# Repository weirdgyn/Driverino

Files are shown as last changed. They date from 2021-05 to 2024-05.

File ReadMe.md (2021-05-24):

# Driverino 

### (italian noun) /ˈdraɪvərnəʊ/ : *little driver*

Driverino is a pretty simple, low power, driver for [BLDC](https://en.wikipedia.org/wiki/Brushless_DC_electric_motor) sensored motors.
The project target was to create a very small unit capable of driving a motor rated about 50-100W.
The board is fitted with ATmega32U4 micro the same of Arduino Micro Pro commercial boards, once the correct bootloader has been burned-in the board should act as an Arduino board (at least for programming/debugging task) and also spin a motor.
The project includes:
 1. Fully designed 2 layers PCB board (KiCAD);
 2. Driverino firmware sources;
 3. MCT8316Z library sources.

Driverino's firmware allow users to drive BLDC motors using a standard [RS232](https://en.wikipedia.org/wiki/RS-232) interface trough simple interactive commands.
The firmware allows also:
* closed loop speed control (implementing a [PID](https://en.wikipedia.org/wiki/PID_controller) loop);
* motor/driver status monitoring;
* R/C ESC emulation.

The library allows Arduino users to interact with BLDC motors without knowledge of MCT8316Z chip and [SPI](https://en.wikipedia.org/wiki/Serial_Peripheral_Interface) protocol.

## Driverino features

* ATmega32U4 microcontroller;
* Micro [USB](https://en.wikipedia.org/wiki/USB) interface;
* MCT8316Z motor driver;
* 41x26mm (size);
* RS232 interface;
* Standard R/C input compatibile.

The board can drive up to 24V-36V 8A rated sensored BLDC motors and provide 5V power supply (200mA max) mimicking R/C ESC BEC feature.
Driverino supports a variety of different types of [Hall](https://en.wikipedia.org/wiki/Hall_effect_sensor)'s sensors (analog single ended, analog differtial, digital) and also different sensors supply rates (3.3V and 5V). To correctly fit for a specific sensor kind some soldering may be required: by default the board project is fitted for digital 5V sensors.

## Firmware

TBD

## Library

TBD

# TODO:

- [ ] Add features:
   - [ ] vm measurement;
   - [ ] current measurement (via INA250).
- [ ] Optimize PCB layout.
- [ ] Write Library.
- [ ] Write Firmware.
- [ ] Submit to Kitspace
- [ ] Submit to Made-With-KiCAD

# Links

* [Atmel/Microchip ATMega32U4](https://www.microchip.com/wwwproducts/en/ATmega32U4)
* [TI MCT8316Z](https://www.ti.com/product/MCT8316Z?keyMatch=MCT8316Z&tisearch=search-everything)
* [Arduino](https://www.arduino.cc/)
* [KiCAD](https://www.kicad.org/)

#

Live long and prosper!

That's all folks.

By[t]e{s} Weirdgyn

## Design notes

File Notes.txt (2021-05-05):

C15 10uF 50V X7R (1206) -> 35V X5R (0805)

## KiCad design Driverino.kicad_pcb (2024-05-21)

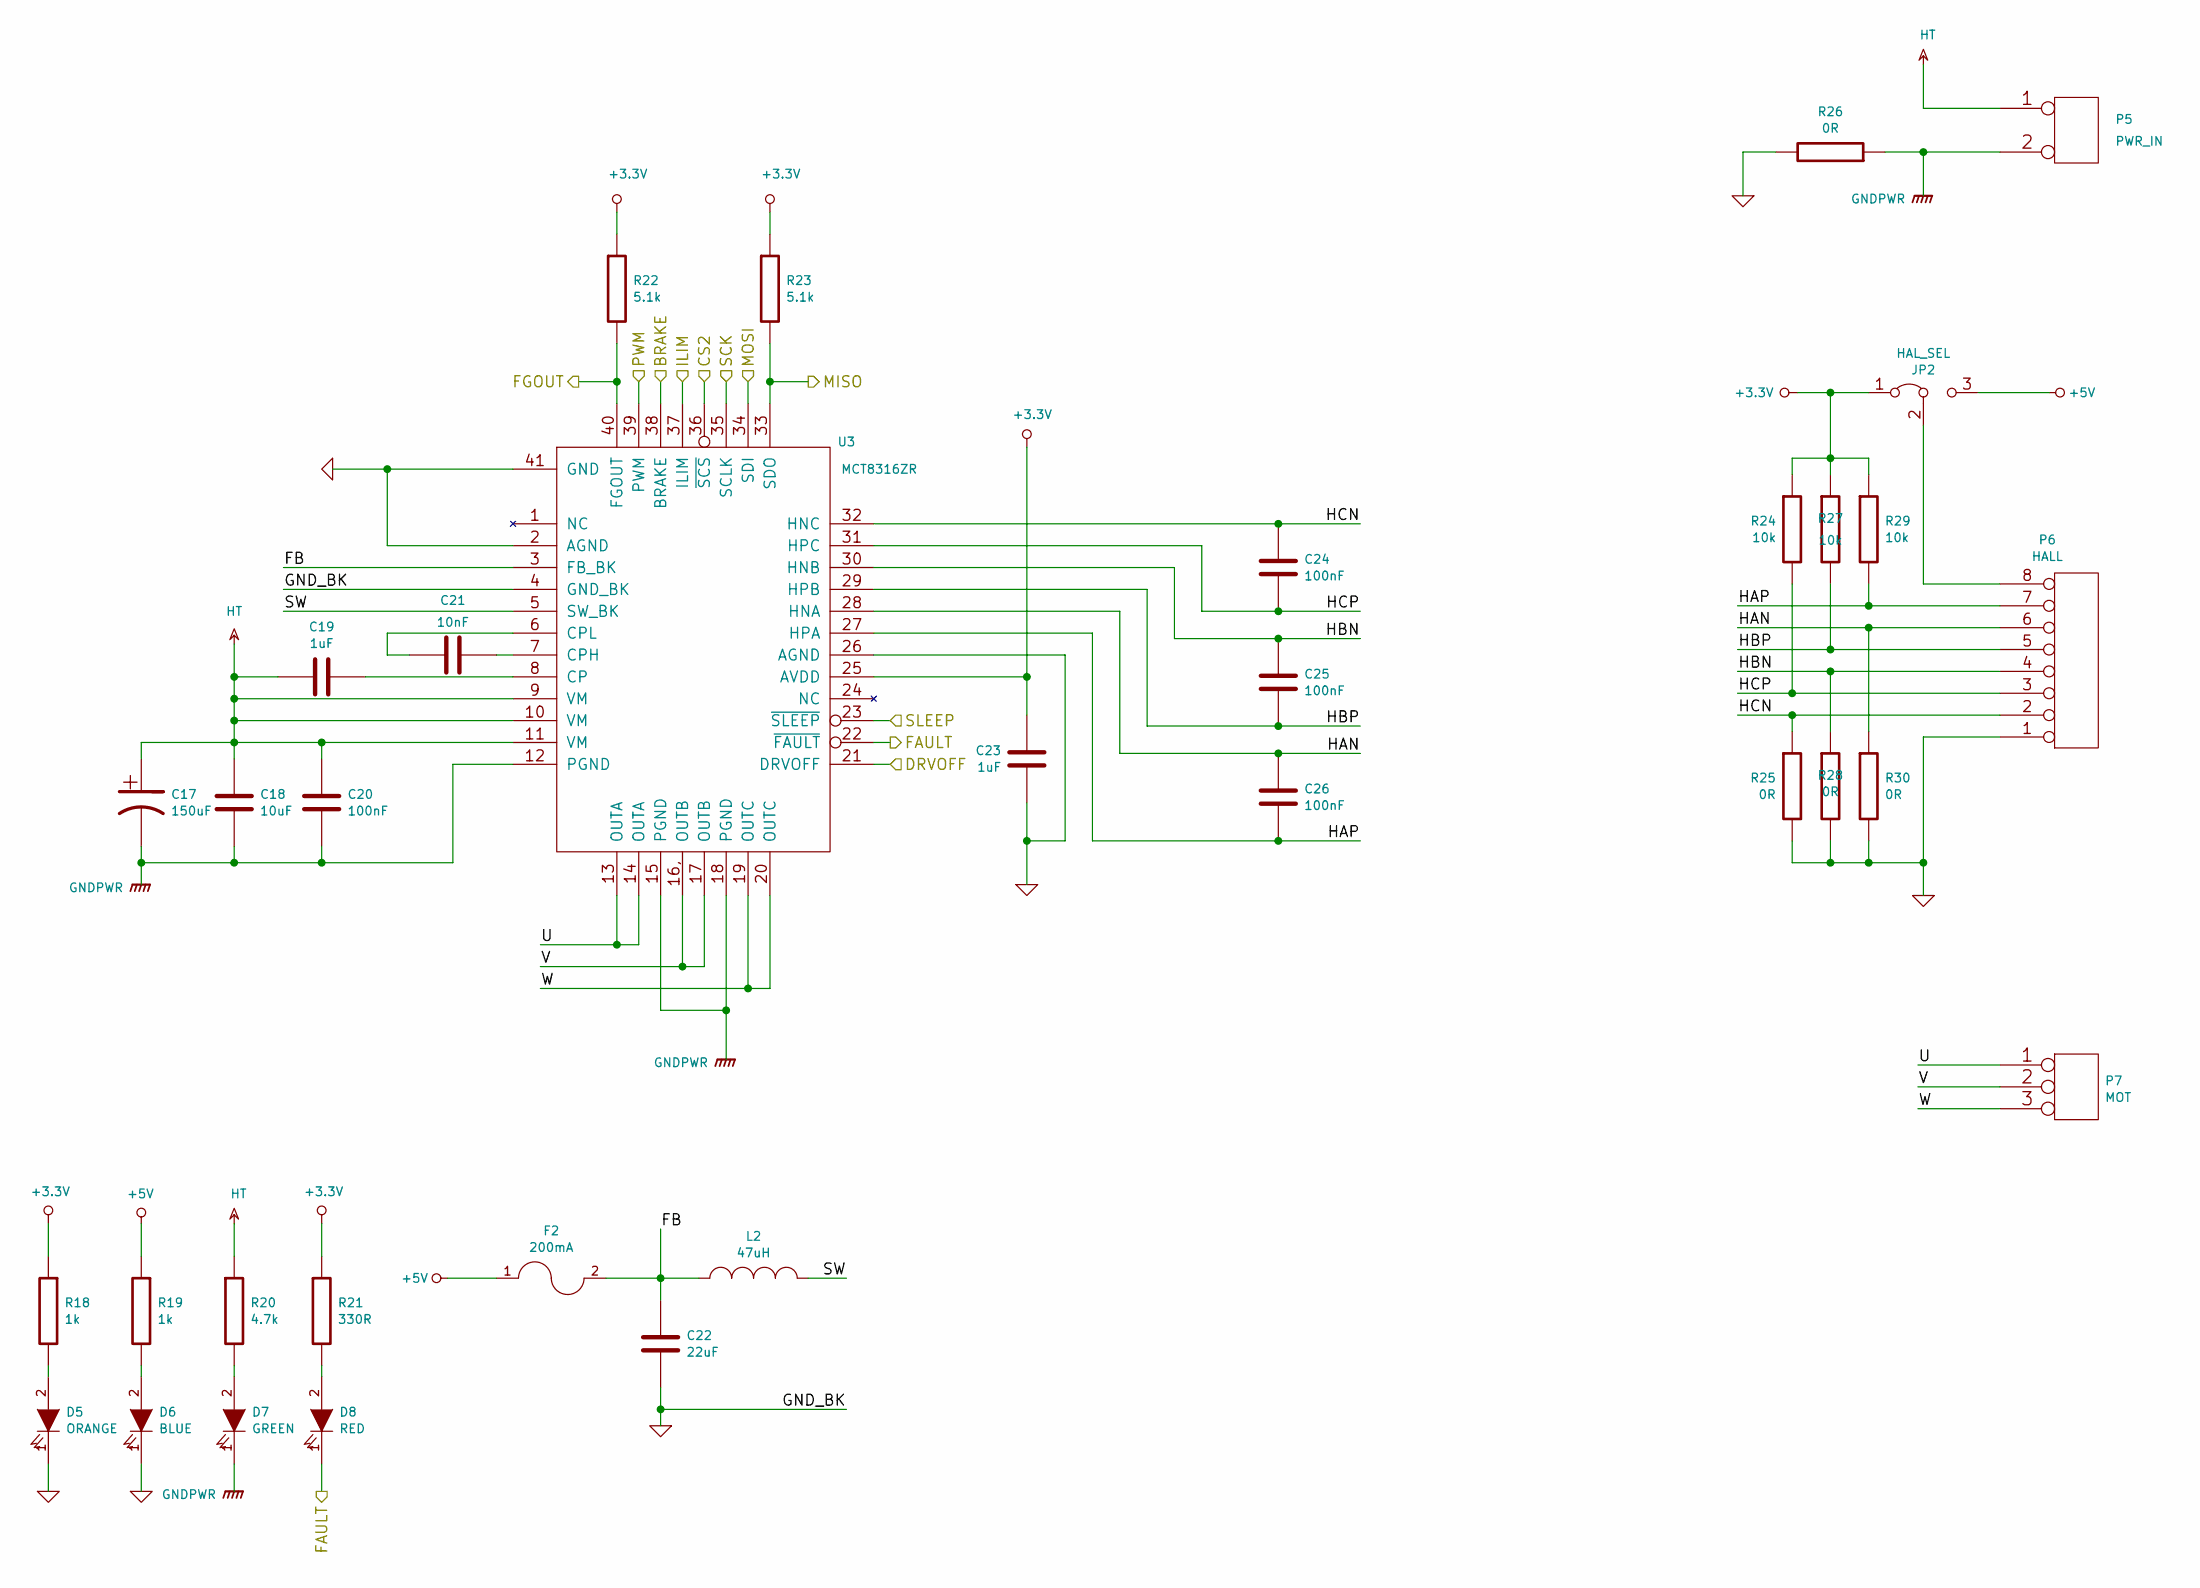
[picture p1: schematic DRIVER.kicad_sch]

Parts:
C17: 150uF; CP_Elec_6.3x7.7
C18: 10uF; C_1206_3216Metric
C19, C23: 1uF; C_0603_1608Metric
C20, C24, C25, C26: 100nF; C_0402_1005Metric
C21: 10nF; C_0402_1005Metric
C22: 22uF; C_1206_3216Metric
D5: ORANGE; LED_0603_1608Metric
D6: BLUE; LED_0603_1608Metric
D7: GREEN; LED_0603_1608Metric
D8: RED; LED_0603_1608Metric
F2: 200mA; Fuse_0402_1005Metric
JP2: HAL_SEL; PinHeader_1x03_P1.27mm_Vertical
L2: 47uH; L_1210_3225Metric
P5: PWR_IN; 39773-0002
P6: HALL; Molex_PicoBlade_53047-0810_1x08_P1.25mm_Vertical
P7: MOT; 39773-0003
R18, R19: 1k; R_0402_1005Metric
R20: 4.7k; R_0402_1005Metric
R21: 330R; R_0402_1005Metric
R22, R23: 5.1k; R_0402_1005Metric
R24, R27, R29: 10k; R_0402_1005Metric
R25, R26, R28, R30: 0R; R_0402_1005Metric
U3: MCT8316ZR; QFN-40_EP_5x7_Pitch0.5mm

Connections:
+3.3V: C23.2, JP2.1 (A), R18.1, R21.1, R22.1, R23.1, R24.1, R27.1, R29.1, U3.25 (AVDD)
+5V: F2.1, JP2.3 (B), R19.1; also elsewhere on the board
/ARDUINO-MICRO/BRAKE: U3.38 (BRAKE); also elsewhere on the board
/ARDUINO-MICRO/CS2: U3.36 (~SCS); also elsewhere on the board
/ARDUINO-MICRO/DRVOFF: U3.21 (DRVOFF); also elsewhere on the board
/ARDUINO-MICRO/FAULT: D8.1 (K), U3.22 (~FAULT); also elsewhere on the board
/ARDUINO-MICRO/FGOUT: R22.2, U3.40 (FGOUT); also elsewhere on the board
/ARDUINO-MICRO/ILIM: U3.37 (ILIM); also elsewhere on the board
/ARDUINO-MICRO/MISO: R23.2, U3.33 (SDO); also elsewhere on the board
/ARDUINO-MICRO/MOSI: U3.34 (SDI); also elsewhere on the board
/ARDUINO-MICRO/PWM: U3.39 (PWM); also elsewhere on the board
/ARDUINO-MICRO/SCK: U3.35 (SCLK); also elsewhere on the board
/DRIVER/FB: C22.2, F2.2, L2.2, U3.3 (FB_BK)
/DRIVER/HAN: C26.2, P6.6, R30.1, U3.28 (HNA)
/DRIVER/HAP: C26.1, P6.7, R29.2, U3.27 (HPA)
/DRIVER/HBN: C25.2, P6.4, R28.1, U3.30 (HNB)
/DRIVER/HBP: C25.1, P6.5, R27.2, U3.29 (HPB)
/DRIVER/HCN: C24.2, P6.2, R25.1, U3.32 (HNC)
/DRIVER/HCP: C24.1, P6.3, R24.2, U3.31 (HPC)
/DRIVER/SLEEP: U3.23 (~SLEEP)
/DRIVER/SW: L2.1, U3.5 (SW_BK)
/DRIVER/U: P7.1, U3.13 (OUTA), U3.14 (OUTA)
/DRIVER/V: P7.2 (PM), U3.16, U3.16, (OUTB), U3.17 (OUTB)
/DRIVER/W: P7.3, U3.19 (OUTC), U3.20 (OUTC)
GND: C22.1, C23.1, D5.1 (K), D6.1 (K), P6.1, R25.2, R26.2, R28.2, R30.2, U3.2 (AGND), U3.4 (GND_BK), U3.26 (AGND), U3.41 (GND); also elsewhere on the board
GNDPWR: C17.2, C18.2, C20.2, D7.1 (K), P5.2 (PM), R26.1, U3.12 (PGND), U3.15 (PGND), U3.18 (PGND)
HT: C17.1, C18.1, C19.2, C20.1, P5.1, R20.1, U3.9 (VM), U3.10 (VM), U3.11 (VM)
unnamed: C19.1, U3.8 (CP)
unnamed: C21.1, U3.7 (CPH)
unnamed: C21.2, U3.6 (CPL)
unnamed: D5.2 (A), R18.2
unnamed: D6.2 (A), R19.2
unnamed: D7.2 (A), R20.2
unnamed: D8.2 (A), R21.2
unnamed: JP2.2 (C), P6.8

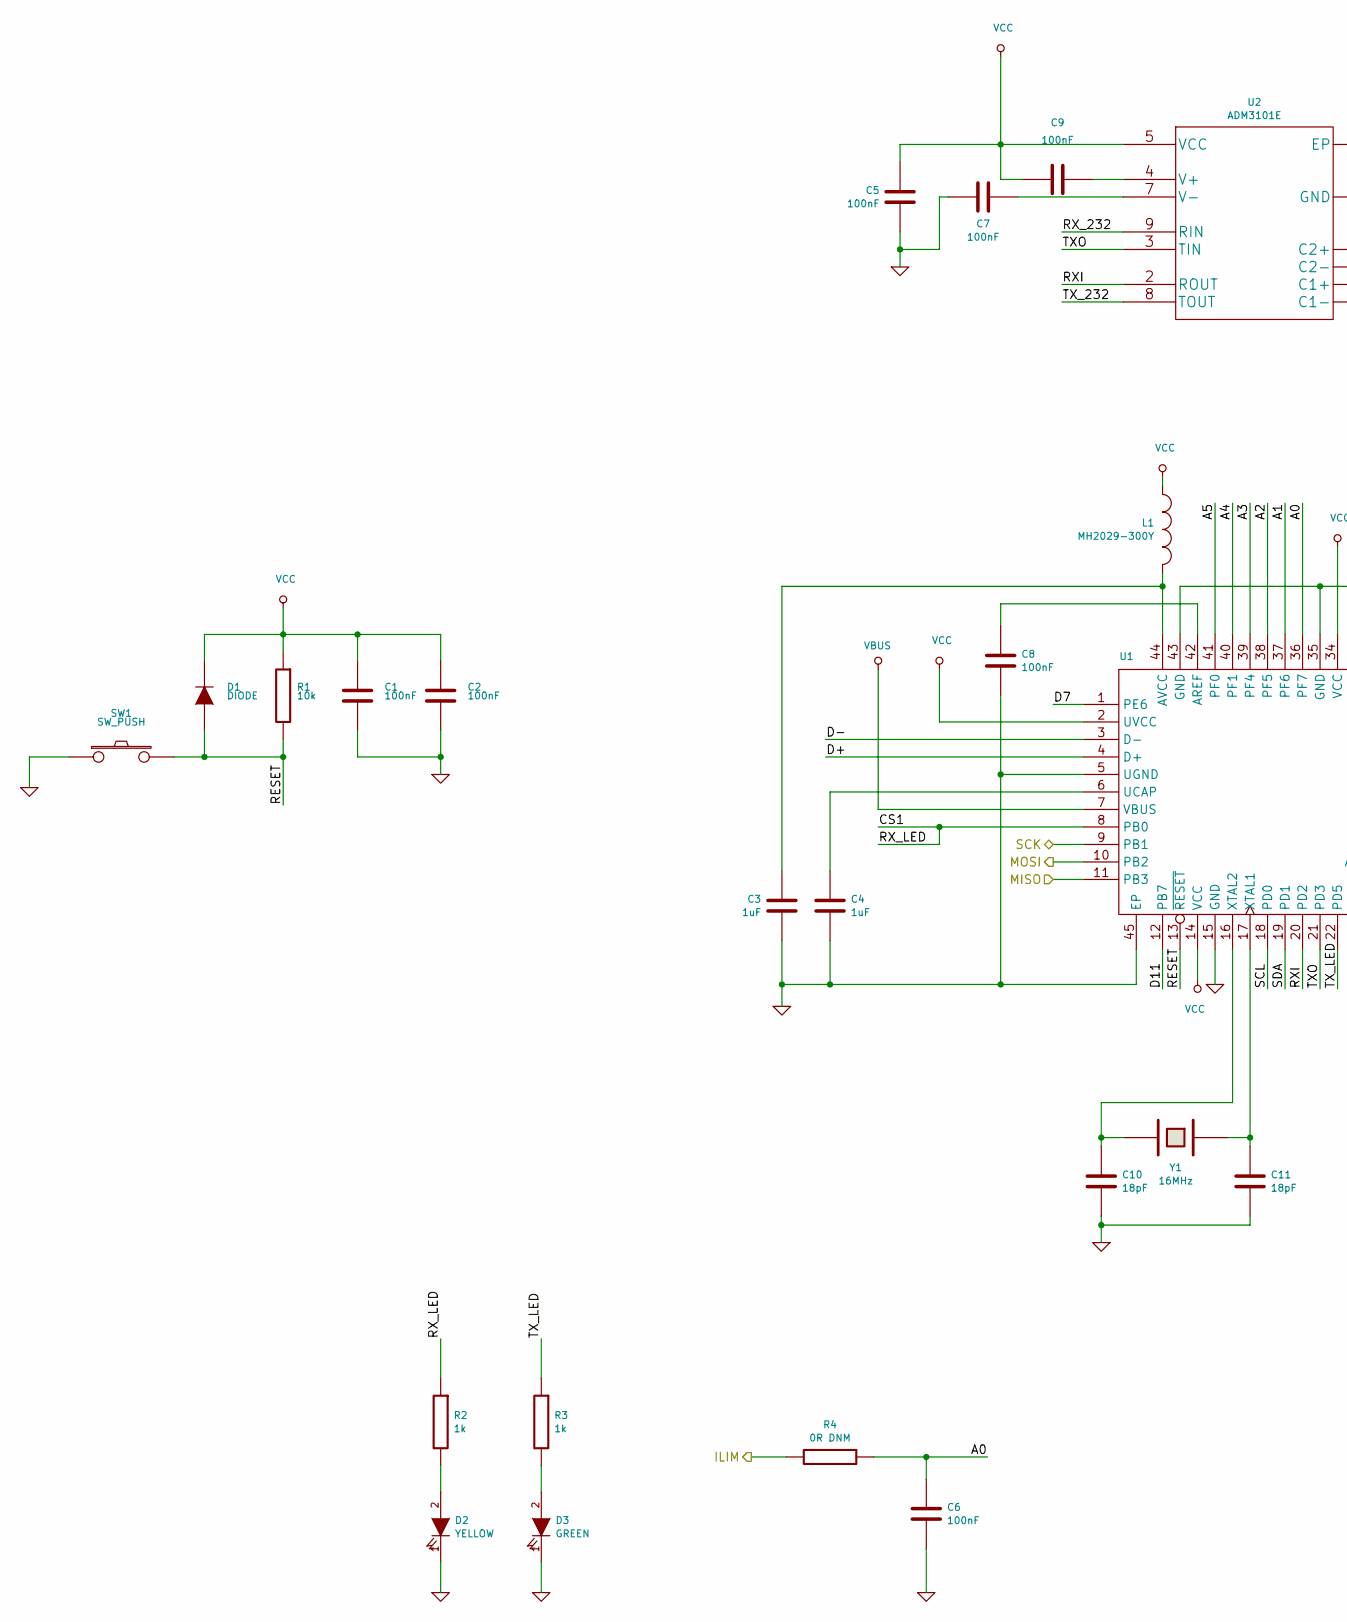
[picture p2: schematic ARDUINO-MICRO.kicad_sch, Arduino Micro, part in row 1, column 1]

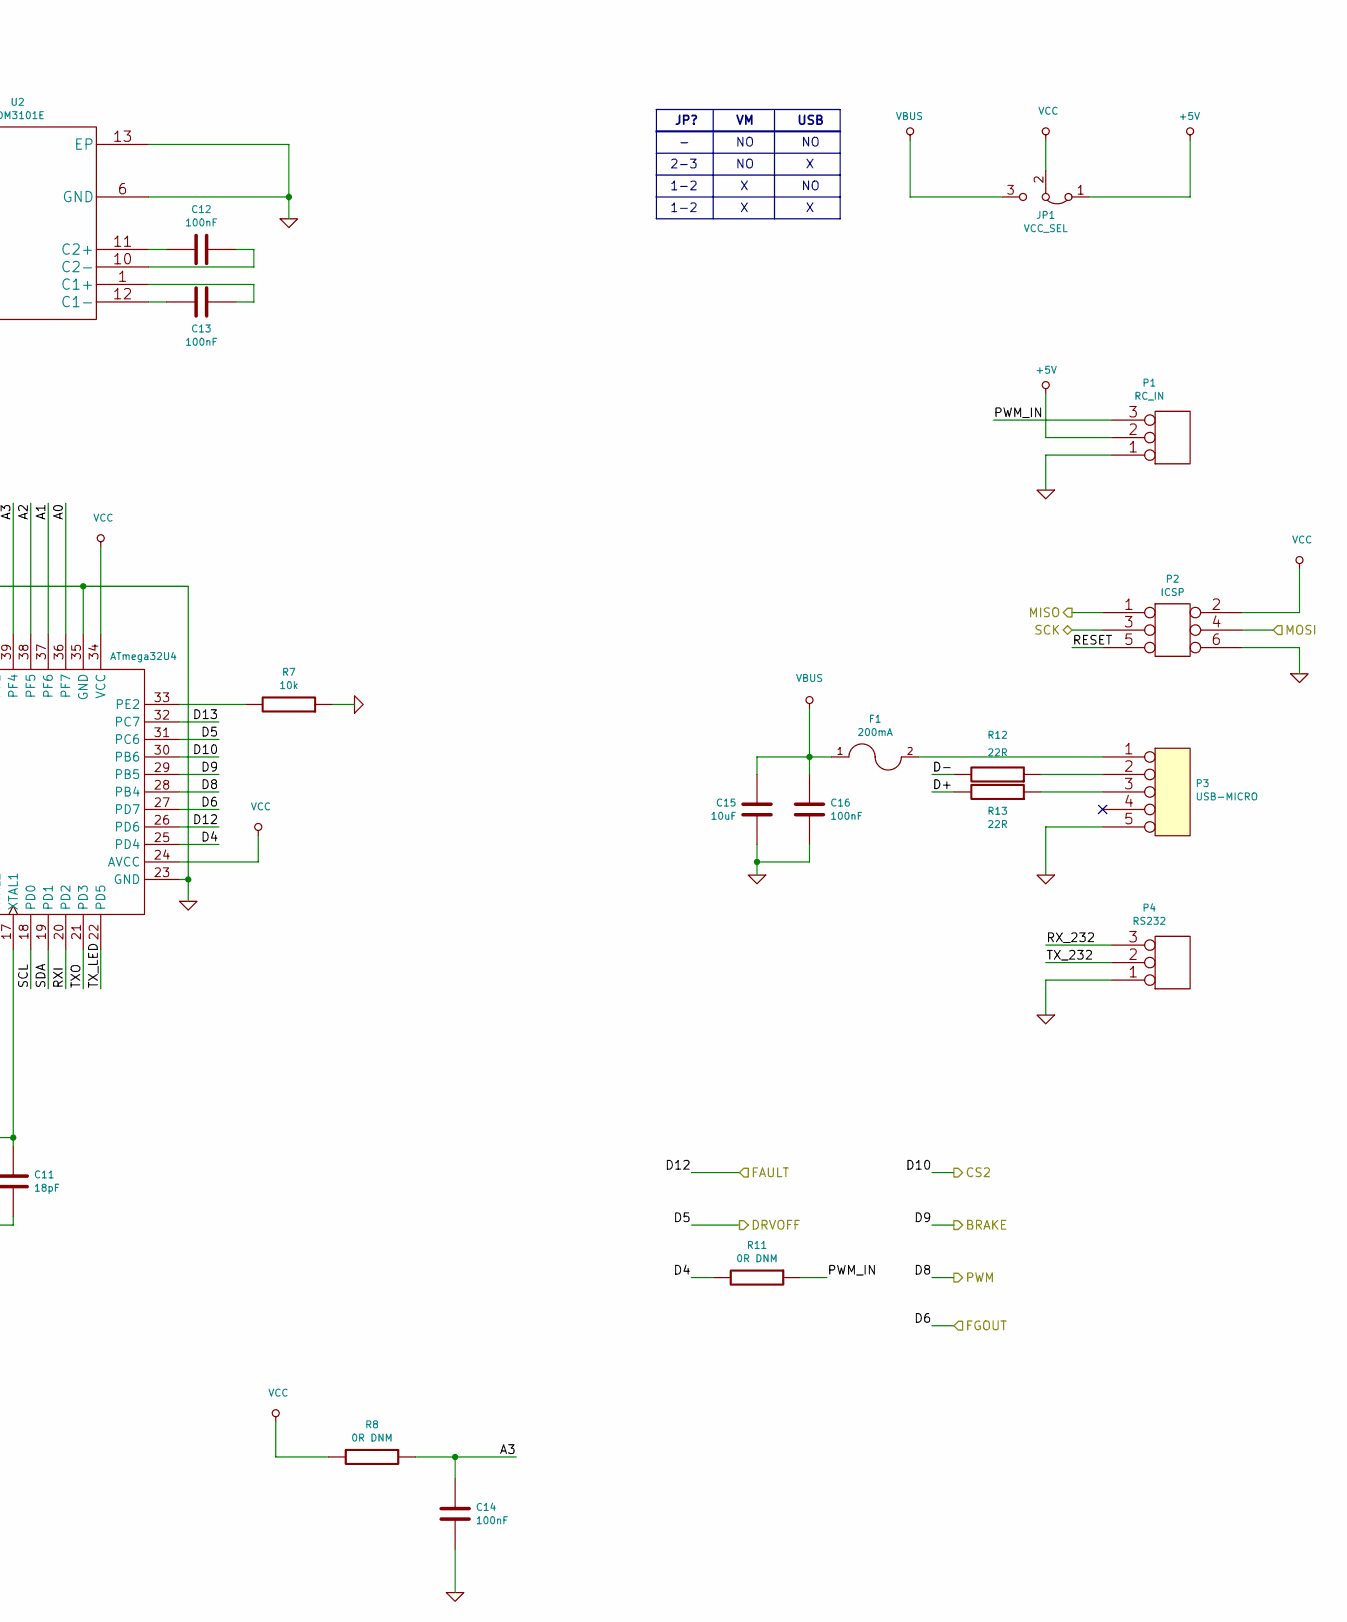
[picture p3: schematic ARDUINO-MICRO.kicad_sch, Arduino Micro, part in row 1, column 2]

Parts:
C1, C2, C5, C6, C7, C8, C9, C12, C13, C14, C16: 100nF; C_0402_1005Metric
C3, C4: 1uF; C_0603_1608Metric
C10, C11: 18pF; C_0402_1005Metric
C15: 10uF; C_1206_3216Metric
D1: DIODE; D_0402_1005Metric
D2: YELLOW; LED_0603_1608Metric
D3: GREEN; LED_0603_1608Metric
F1: 200mA; Fuse_0402_1005Metric
JP1: VCC_SEL; PinHeader_1x03_P1.27mm_Vertical
L1: MH2029-300Y; R_0805_2012Metric
P1: RC_IN; PinHeader_1x03_P2.54mm_Horizontal
P2: ICSP; PinHeader_2x03_P2.54mm_Vertical
P3: USB-MICRO; USB_Micro-B_Amphenol_10103594-0001LF_Horizontal
P4: RS232; Molex_PicoBlade_53047-0310_1x03_P1.25mm_Vertical
R1, R7: 10k; R_0402_1005Metric
R2, R3: 1k; R_0402_1005Metric
R4, R8, R11: 0R DNM; R_0402_1005Metric
R12, R13: 22R; R_0402_1005Metric
SW1: SW_PUSH; SW_SPST_B3U-1000P
U1: ATmega32U4; QFN-44-1EP_7x7mm_P0.5mm_EP5.2x5.2mm
U2: ADM3101E; CP-12-4
Y1: 16MHz; Crystal_SMD_2016-4Pin_2.0x1.6mm

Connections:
+5V: JP1.1 (A), P1.2 (PM); also elsewhere on the board
/ARDUINO-MICRO/A0: C6.2, R4.1, U1.36 (PF7)
/ARDUINO-MICRO/A1: U1.37 (PF6)
/ARDUINO-MICRO/A2: U1.38 (PF5)
/ARDUINO-MICRO/A3: C14.2, R8.1, U1.39 (PF4)
/ARDUINO-MICRO/A4: U1.40 (PF1)
/ARDUINO-MICRO/A5: U1.41 (PF0)
/ARDUINO-MICRO/BRAKE: U1.29 (PB5); also elsewhere on the board
/ARDUINO-MICRO/CS1: R2.1, U1.8 (PB0)
/ARDUINO-MICRO/CS2: U1.30 (PB6); also elsewhere on the board
/ARDUINO-MICRO/D4: R11.2, U1.25 (PD4)
/ARDUINO-MICRO/D7: U1.1 (PE6)
/ARDUINO-MICRO/D11: U1.12 (PB7)
/ARDUINO-MICRO/D13: U1.32 (PC7)
/ARDUINO-MICRO/D+: R13.2, U1.4 (D+)
/ARDUINO-MICRO/D-: R12.2, U1.3 (D-)
/ARDUINO-MICRO/DRVOFF: U1.31 (PC6); also elsewhere on the board
/ARDUINO-MICRO/FAULT: U1.26 (PD6); also elsewhere on the board
/ARDUINO-MICRO/FGOUT: U1.27 (PD7); also elsewhere on the board
/ARDUINO-MICRO/ILIM: R4.2; also elsewhere on the board
/ARDUINO-MICRO/MISO: P2.1, U1.11 (PB3); also elsewhere on the board
/ARDUINO-MICRO/MOSI: P2.4, U1.10 (PB2); also elsewhere on the board
/ARDUINO-MICRO/PWM: U1.28 (PB4); also elsewhere on the board
/ARDUINO-MICRO/PWM_IN: P1.3, R11.1
/ARDUINO-MICRO/RESET: D1.2 (A), P2.5, R1.2, SW1.2, U1.13 (~RESET)
/ARDUINO-MICRO/RXI: U1.20 (PD2), U2.2 (ROUT)
/ARDUINO-MICRO/RX_232: P4.3, U2.9 (RIN)
/ARDUINO-MICRO/SCK: P2.3, U1.9 (PB1); also elsewhere on the board
/ARDUINO-MICRO/SCL: U1.18 (PD0)
/ARDUINO-MICRO/SDA: U1.19 (PD1)
/ARDUINO-MICRO/TXO: U1.21 (PD3), U2.3 (TIN)
/ARDUINO-MICRO/TX_232: P4.2 (PM), U2.8 (TOUT)
/ARDUINO-MICRO/TX_LED: R3.1, U1.22 (PD5)
GND: C1.1, C2.1, C3.1, C4.1, C5.2, C6.1, C7.2, C8.1, C10.2, C11.2, C14.1, C15.1, C16.1, D2.1 (K), D3.1 (K), P1.1, P2.6, P3.5, P4.1, R7.1, SW1.1, U1.5 (UGND), U1.15 (GND), U1.23 (GND), U1.35 (GND), U1.43 (GND), U1.45 (EP), U2.6 (GND), U2.13 (EP); also elsewhere on the board
unnamed: C3.2, L1.2, U1.44 (AVCC)
unnamed: C4.2, U1.6 (UCAP)
unnamed: C7.1, U2.7 (V-)
unnamed: C8.2, U1.42 (AREF)
unnamed: C9.2, U2.4 (V+)
unnamed: C10.1, U1.16 (XTAL2), Y1.2
unnamed: C11.1, U1.17 (XTAL1), Y1.1
unnamed: C12.1, U2.10 (C2-)
unnamed: C12.2, U2.11 (C2+)
unnamed: C13.1, U2.1 (C1+)
unnamed: C13.2, U2.12 (C1-)
unnamed: D2.2 (A), R2.2
unnamed: D3.2 (A), R3.2
unnamed: F1.2, P3.1
unnamed: P3.2, R12.1
unnamed: P3.3, R13.1
unnamed: R7.2, U1.33 (PE2)
VBUS: C15.2, C16.2, F1.1, JP1.3 (B), U1.7 (VBUS)
VCC: C1.2, C2.2, C5.1, C9.1, D1.1 (K), JP1.2 (C), L1.1, P2.2, R1.1, R8.2, U1.2 (UVCC), U1.14 (VCC), U1.24 (AVCC), U1.34 (VCC), U2.5 (VCC)

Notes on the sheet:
1-2
JP?
2-3
USB

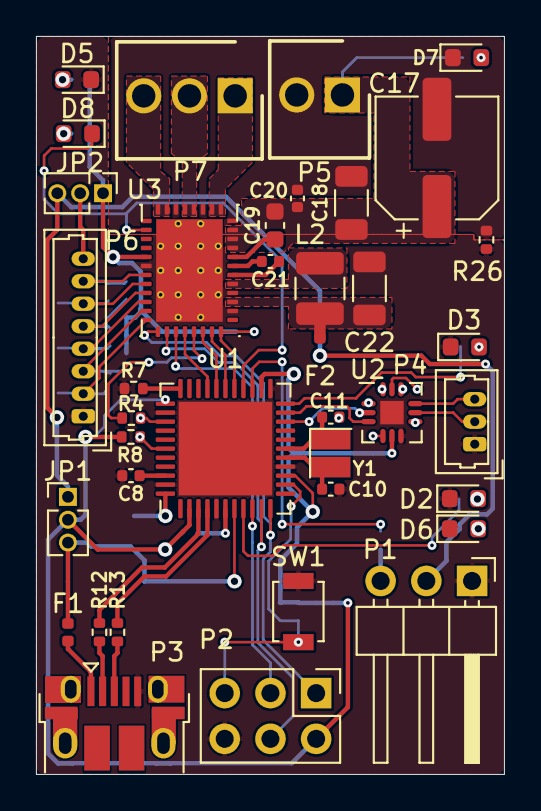
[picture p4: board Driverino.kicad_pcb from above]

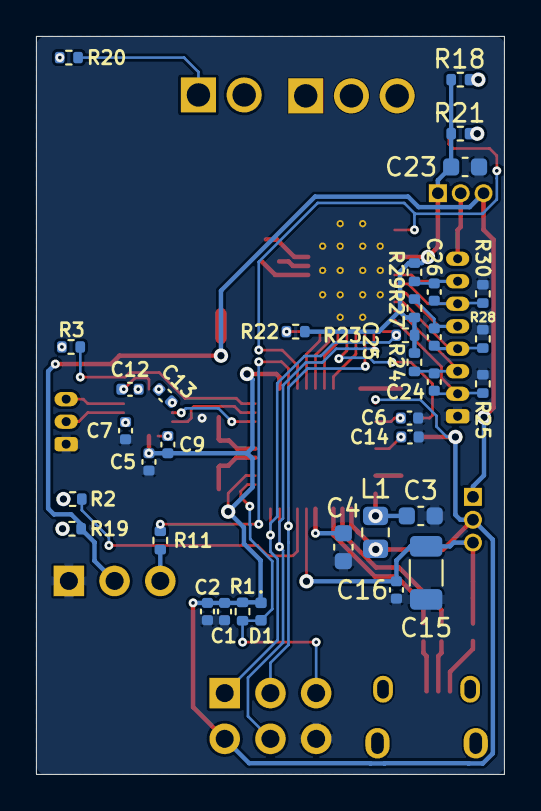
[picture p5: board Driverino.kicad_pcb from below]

Board: 2 copper layers, 26.0 x 41.0 mm, 73 parts (35 on the bottom side), 66 nets.

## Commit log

2021-04-29 Defined schematics hierarchy
    [ARDUINO-MICRO.sch, DRIVER.sch, Driverino.sch]
2021-05-05 Routing completed
    [Driverino.kicad_pcb]
2021-05-05 Gerber plot
    [Driverino-B_Cu.gbr, Driverino-B_Mask.gbr, Driverino-B_Paste.gbr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]
2021-05-05 Modified F1
    [ARDUINO-MICRO.sch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]
2024-05-21 Update to KiCAD 8.0
    Update to KiCAD 8.0
    [ARDUINO-MICRO.kicad_sch, ARDUINO-MICRO.sch, DRIVER.kicad_sch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]

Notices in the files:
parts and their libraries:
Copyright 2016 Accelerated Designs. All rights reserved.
